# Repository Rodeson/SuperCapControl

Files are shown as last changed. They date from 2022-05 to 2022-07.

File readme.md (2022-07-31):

README For SuperCapControl

超级电容 ultracapacitor

@Rodeson

Email：lds947003754@outlook.com

## 0.超级电容图片说明

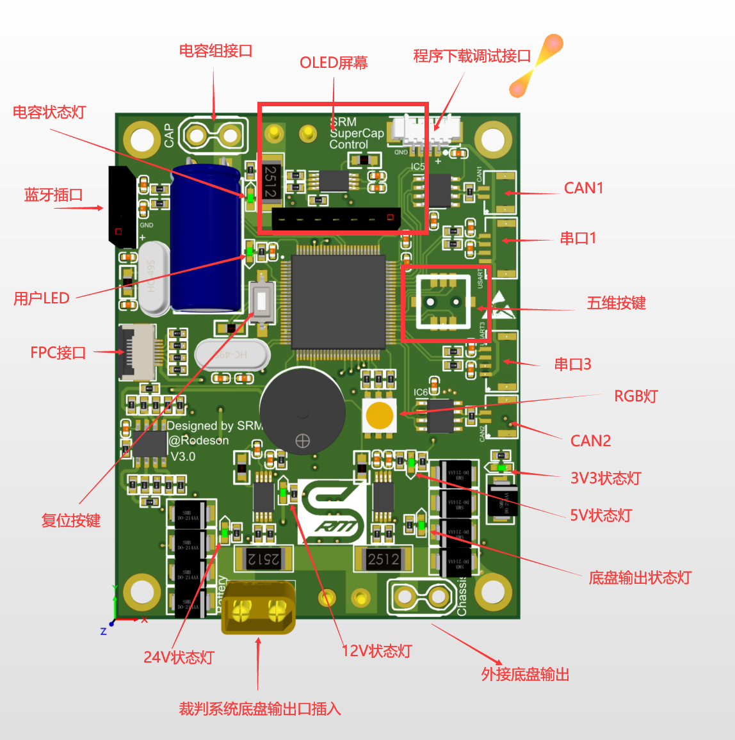
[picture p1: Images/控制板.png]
控制板
### 控制板

### 功率板

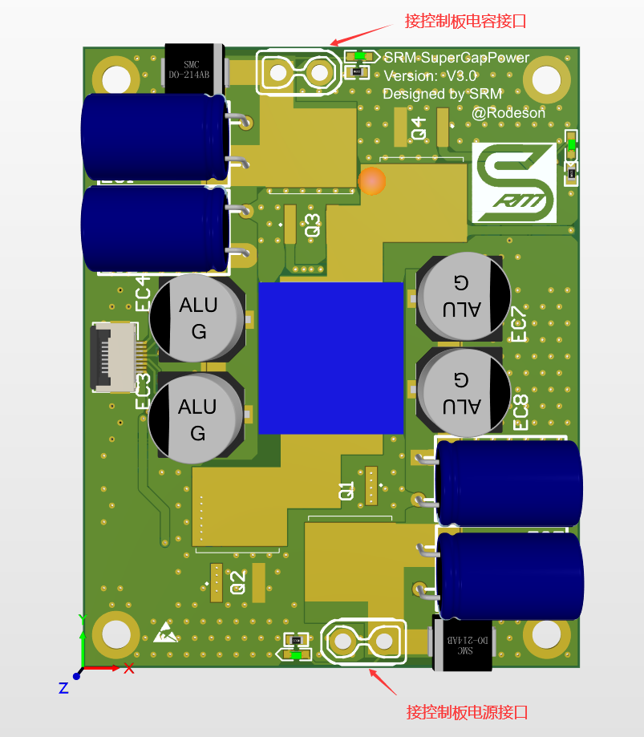
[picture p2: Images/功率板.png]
功率板


### 组合渲染图像

控制板功率板

SuperCapPCB

电容组

capacitor

## 1.超级电容硬件说明

1. 使用4Buckboost电路，实现升降压控制。
2. 将控制板和功率板进行拆分设计，两个板子对应接口固定，PWM控制线通过FPC排线连接，电源接口使用XT30接口连接。
3. 更改设计后，V2.0板子实际面积更小，在舵轮上安装方便。
4. 在实际使用过程中，为方便了解超级电容工作状态，视觉上增加RGB灯显示板子工作情况，听觉上增加蜂鸣器，能够在工作异常时第一时间了解情况。
5. 传感器选型上使用ina240a1和opa2350ua，使用adc读取模拟信号，上一代超级电容使用ina226容易出现i2c通信掉线情况。
6. 增加板载温度传感器MCP9700AT-E_TT，监测超级电容工作温度。
7. PCB设计时，减小PCB上大电流走线距离，板载大电流开窗布线。
8. 增加可交互的五维按键和OLED显示屏，方便现场调参。

## 2.硬件设计

### 2.1 采样电路

2.1.1接口采样电路

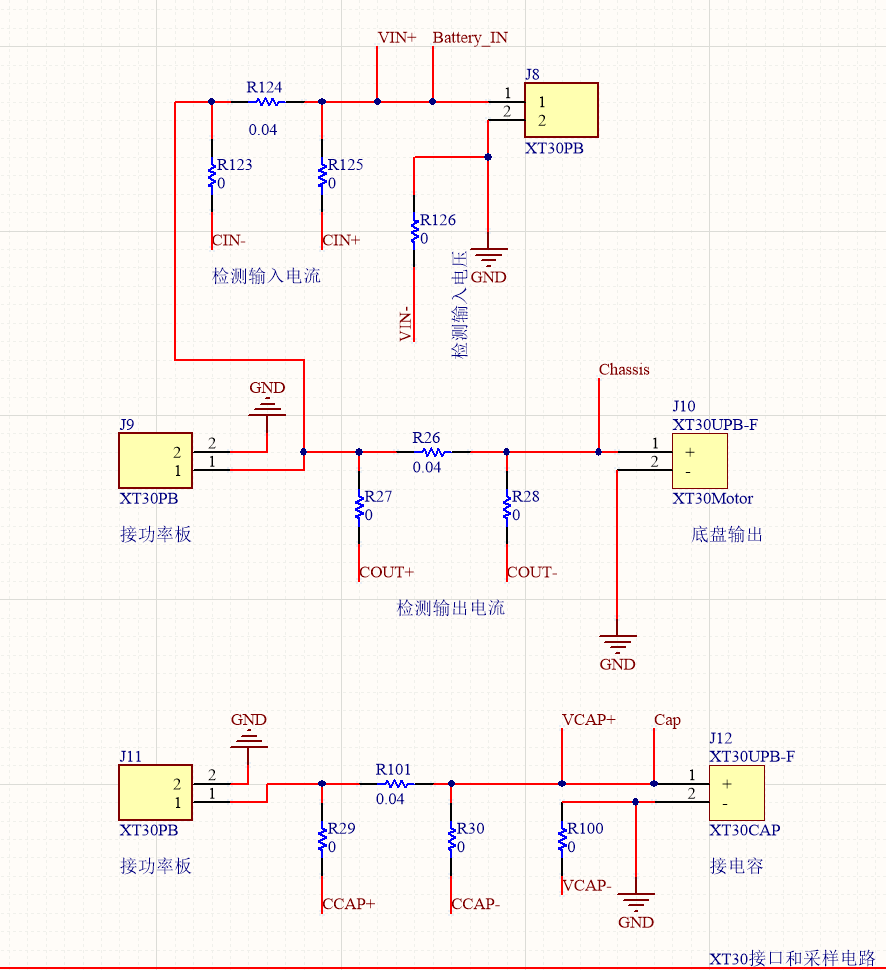
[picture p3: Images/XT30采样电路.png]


2.1.2电流传感器

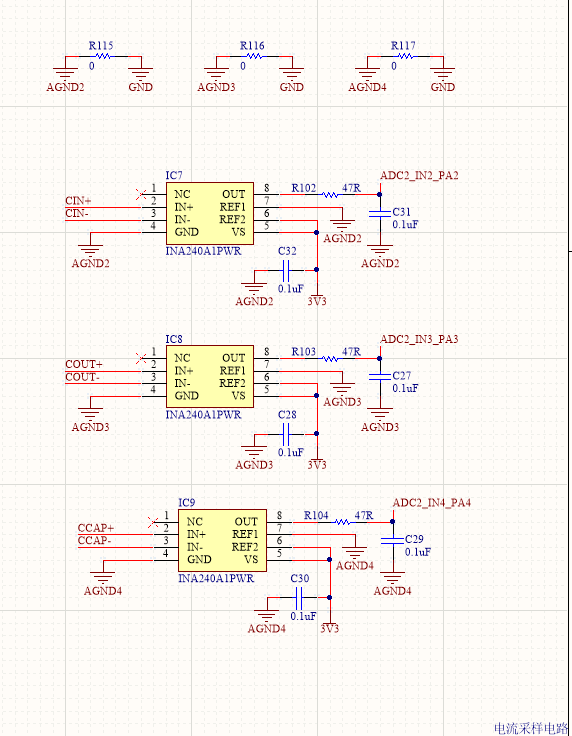
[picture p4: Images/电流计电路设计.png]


2.1.3电压传感器

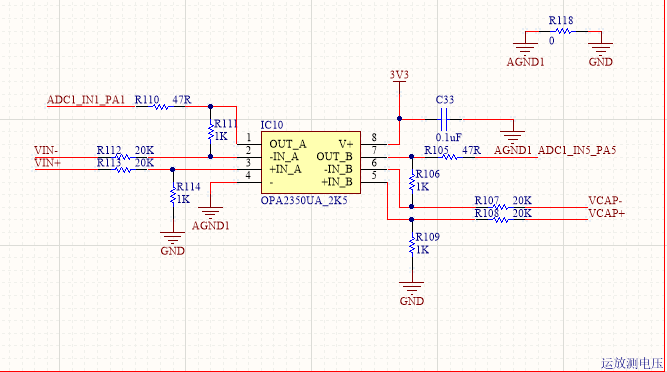
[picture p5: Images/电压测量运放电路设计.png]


### 2.2 BuckBoost电路

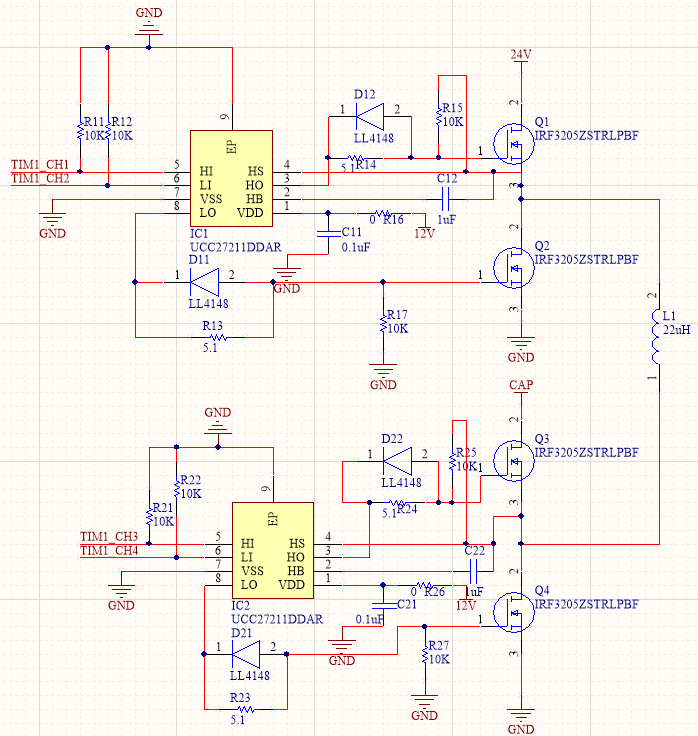
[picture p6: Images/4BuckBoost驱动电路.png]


### 2.3供电路径

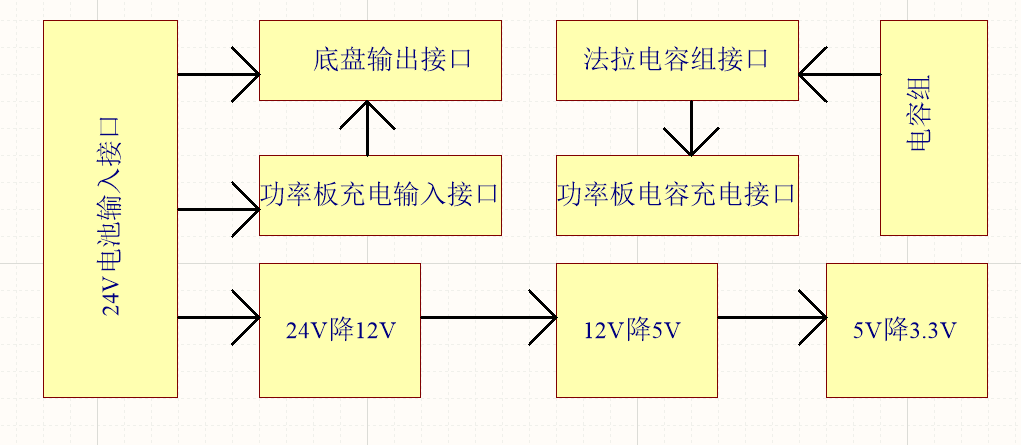
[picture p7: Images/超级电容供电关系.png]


## 3.超级电容控制思路

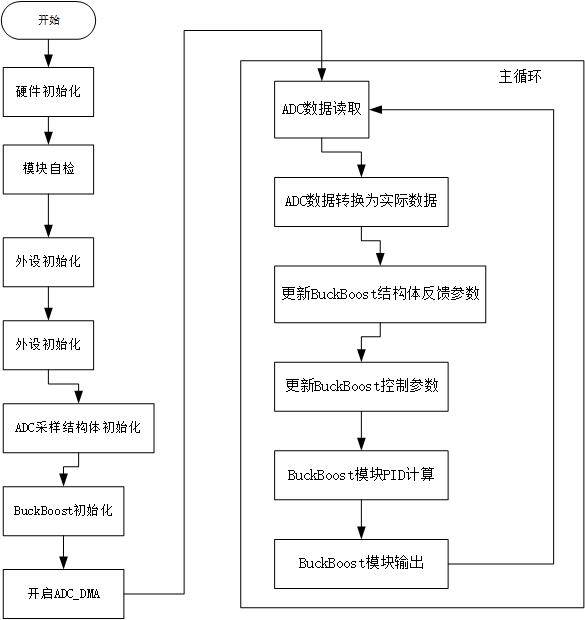
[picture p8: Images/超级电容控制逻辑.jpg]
超级电容控制逻辑


## 4.超级电容buckboost模块控制逻辑

### 4.1采样数据计算

```c
    battery_in.I_now = buckboost_control.BUCKBOOST_IN_C;
    battery_in.U_now = buckboost_control.BUCKBOOST_IN_V;
    battery_in.P_now = battery_in.I_now * battery_in.U_now;

    chassis_out.I_now = buckboost_control.BUCKBOOST_OUT_C;
    chassis_out.U_now = buckboost_control.BUCKBOOST_IN_V;
    chassis_out.P_now = chassis_out.I_now * chassis_out.U_now;

    dcdc_in.I_now = buckboost_control.BUCKBOOST_IN_C - buckboost_control.BUCKBOOST_OUT_C;
    dcdc_in.U_now = buckboost_control.BUCKBOOST_IN_V;
    dcdc_in.P_now = dcdc_in.I_now * dcdc_in.U_now;

    dcdc_out.I_now = buckboost_control.BUCKBOOST_CAP_C;
    dcdc_out.U_now = buckboost_control.BUCKBOOST_CAP_V;
    dcdc_out.P_now = buckboost_control.BUCKBOOST_CAP_C * buckboost_control.BUCKBOOST_CAP_V;
```

### 4.2串级PID思路

#### 4.2.1缓冲能量环

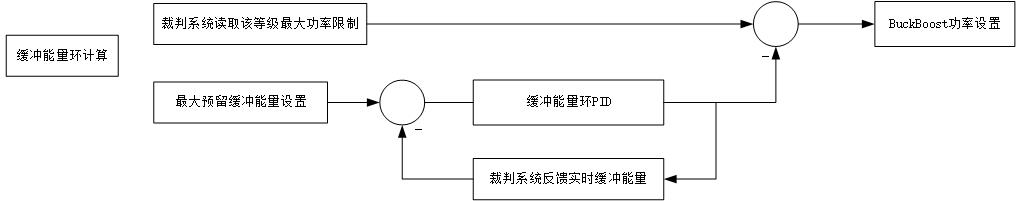
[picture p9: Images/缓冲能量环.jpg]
缓冲能量环


#### 4.2.2功率环

功率环

#### 4.2.3电压电流环

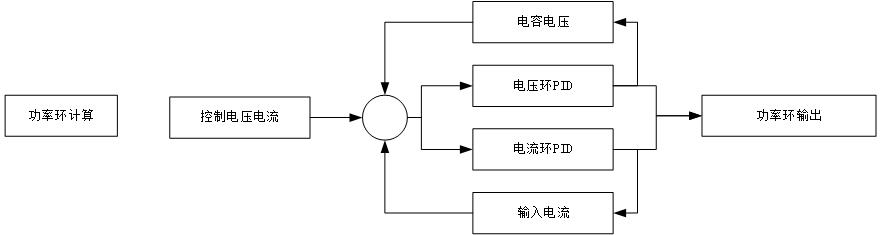
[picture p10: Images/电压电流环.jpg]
电压电流环


### 4.3输出设置

输出设置

## 5.NMOS挂载情况

```c
/****************************
24V                 CAP
Q1------|     |------Q3
        |-----|
        |  L  |
        |-----|
Q2------|     |------Q4
*****************************/
#define Q1_PWMControl_TIM     htim1
#define Q1_PWMControl_TIM_CH  TIM_CHANNEL_1
#define Q2_PWMControl_TIM     htim1
#define Q2_PWMControl_TIM_CH  TIM_CHANNEL_2
#define Q3_PWMControl_TIM     htim1
#define Q3_PWMControl_TIM_CH  TIM_CHANNEL_3
#define Q4_PWMControl_TIM     htim1
#define Q4_PWMControl_TIM_CH  TIM_CHANNEL_4
```

## 6.BuckBoost控制 C语言结构体

```c
typedef struct
{
  uint8_t data_update;    //1更新
  uint8_t buckboostmode;  //0为初始关闭模式 1为降压模式 2为升压模式
  uint8_t loop_mode;      //环路模式0：cv 1：cc 2：cp
  float efficiency;       //总效率 ，热耗散
  uint8_t power_dir;      //能量方向0正向充电1反向放电
  uint16_t max_power_lim; //裁判系统最大功率
  float power_pass;       //  裁判系统花去功率板与板子测量误差经过pid结果用于传递
  uint8_t referee_power;
  uint8_t referee_buff;
  float powerbuffer ;     //缓冲能量
    
  PID_Regulator_t BuckBoostLoopCcompare_PID;//输出电流环
  PID_Regulator_t BuckBoostLoopVcompare_PID;//输出电压环
  PID_Regulator_t Robot_Buffer_PID;//缓冲能量环
  PID_Regulator_t Robot_Power_PID;//功率环

  double BUCKBOOST_CAP_C;
  double BUCKBOOST_CAP_V;
  double BUCKBOOST_IN_C;
  double BUCKBOOST_IN_V;
  double BUCKBOOST_OUT_C;
    
  double BUCKBOOST_NEED_C;
        
  float BUCKBOOST_IN_P;
  float BUCKBOOST_OUT_P;
  float BUCKBOOST_CAP_P;
  float BUCKBOOST_NEED_P;
  
  float charge_power;//功率环计算OUT
  float charge_current;// = charge_power/inV
  float cloop;
  float vloop;
  float ratio_pass;//计算升降压比例

  uint8_t POWER_LIMIT_MODE;//超级电容功率限制模式 0使用电容 1不使用电容
    
} BUCKBOOST_STRUCT;
```

## 7.超级电容模块通信协议

### 7.1CAN 发送程序参考

发送函数

```c
void supercap_sendmessage(uint16_t Vcap)
{
		static uint8_t supercap_tx_data[2];
	
		Tx1Message.StdId=0x211;
		Tx1Message.IDE =CAN_ID_STD;
		Tx1Message.RTR=CAN_RTR_DATA;
		Tx1Message.DLC =0x08;
		memcpy (supercap_tx_data, &Vcap, sizeof(Vcap));
		HAL_CAN_AddTxMessage(&hcan1, &Tx1Message, supercap_tx_data ,&pTxMailbox);
}
```

实例应用（发送超级电容电压数据 由于是无符号16位整数 因此需要将浮点数乘以1000并发送整数）

```c
supercap_sendmessage(buckboost_control.BUCKBOOST_CAP_V * 1000);
```

### 7.2CAN 接收程序参考

接收函数（接收裁判系统底盘参数 为当前等级底盘最大功率及实时缓冲能量）

```c
void get_supercap_measure(BUCKBOOST_STRUCT *cap, uint8_t aData[])
{
    cap -> referee_power  = aData[0];
    cap -> referee_buff  = aData[1];
}
```

实例应用（该函数 扔在can线接收中断里面）

```c
void CAN1_Getdata(CAN_RxHeaderTypeDef *pHeader,uint8_t aData[])
{
	switch (pHeader->StdId)
	{
		case 0x0210:
		{
			//得到超级电容数据
			get_supercap_measure(&buckboost_control,aData);
		}
		default:
		{
			
		}break;
	}
}
```

## Bug记录

20220731 舵轮No.3 贺道明

问题描述：超级电容上电后，裁判系统电源管理模块直接停止工作，所有供电全部断掉，出现短路现象。但后续重新上电，超级电容模块恢复正常使用。

问题分析：长时间未使用超级电容，导致超级电容电压低于12V。后续上电过程中，进入大电流充电模式，导致电池输出电流较大，电池管理误判断电池短路，触发电池保护机制，断掉电池输出。

问题解决方法：临时解决方法，使用超级电容前，确保超级电容电压高于12V。后续解决方法，程序判断超级电容电压，增加电容低电压充电模式，避免上电后大电流充电。（仅限于长时间未使用，电容组电压过低情况）。

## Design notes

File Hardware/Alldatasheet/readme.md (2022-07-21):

ALLdatasheet 说明

| IC | | |
| --- | --- | ---- |
| INA225AIDGK | 电流检测芯片 | |
| LMR14020SDDAR | 24V降12V | |
| MP1584EN-LF | 12V降5V | |
| OPA2350UA_2K5 | 运放测电压 | |
| SN65HVD230DR  | CAN线接收 | |
| | | |

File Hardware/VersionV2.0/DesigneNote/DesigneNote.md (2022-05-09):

# DesigneNote

本文档记录设计过程需要修改的地方

Product：SupercapV3Control

Version：20220222

Todo：

1. OLED屏幕换成TFT屏幕 节省空间
2. 减少板载LED个数
3. 将拨码开关换成5维按键

Product：SupercapV3Control

Version：20220224

Update：

1. 新加温度传感器
2. 将拨码开关修改为五维按键
3. 补充MCU五维按键引脚
4. 3V3降压前增加测量点 保护MCU

Product：SupercapV3Power

Version：20220224 

Update：

1. 根据上版本功率板绘制原理图
2. 将排针排母走控制信号方案改为FPC走信号线方案

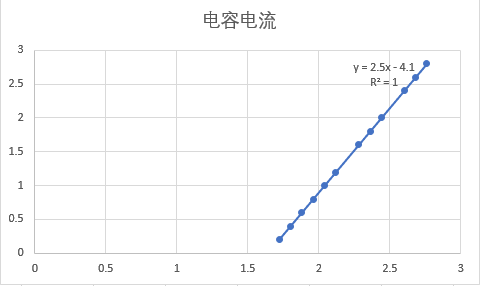
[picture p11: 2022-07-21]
Docs/SupercapNo.3Data/电容电流.png

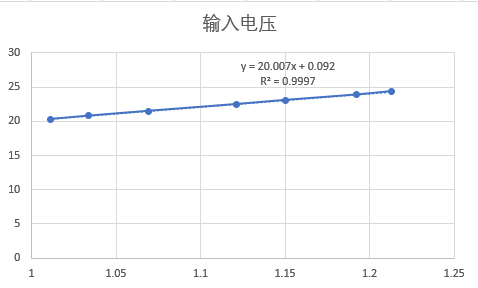
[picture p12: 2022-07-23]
Docs/SupercapNo.7Data/输入电压.png

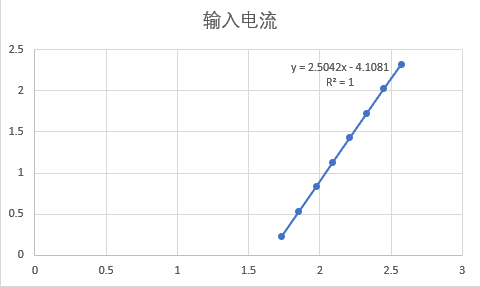
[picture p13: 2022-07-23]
Docs/SupercapNo.7Data/输入电流.png

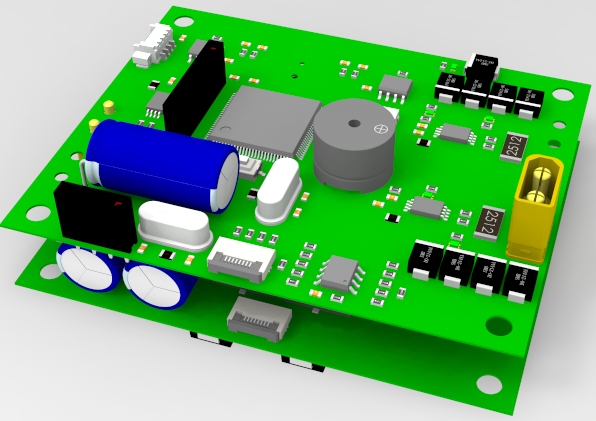
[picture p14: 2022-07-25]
Images/组合渲染图.png

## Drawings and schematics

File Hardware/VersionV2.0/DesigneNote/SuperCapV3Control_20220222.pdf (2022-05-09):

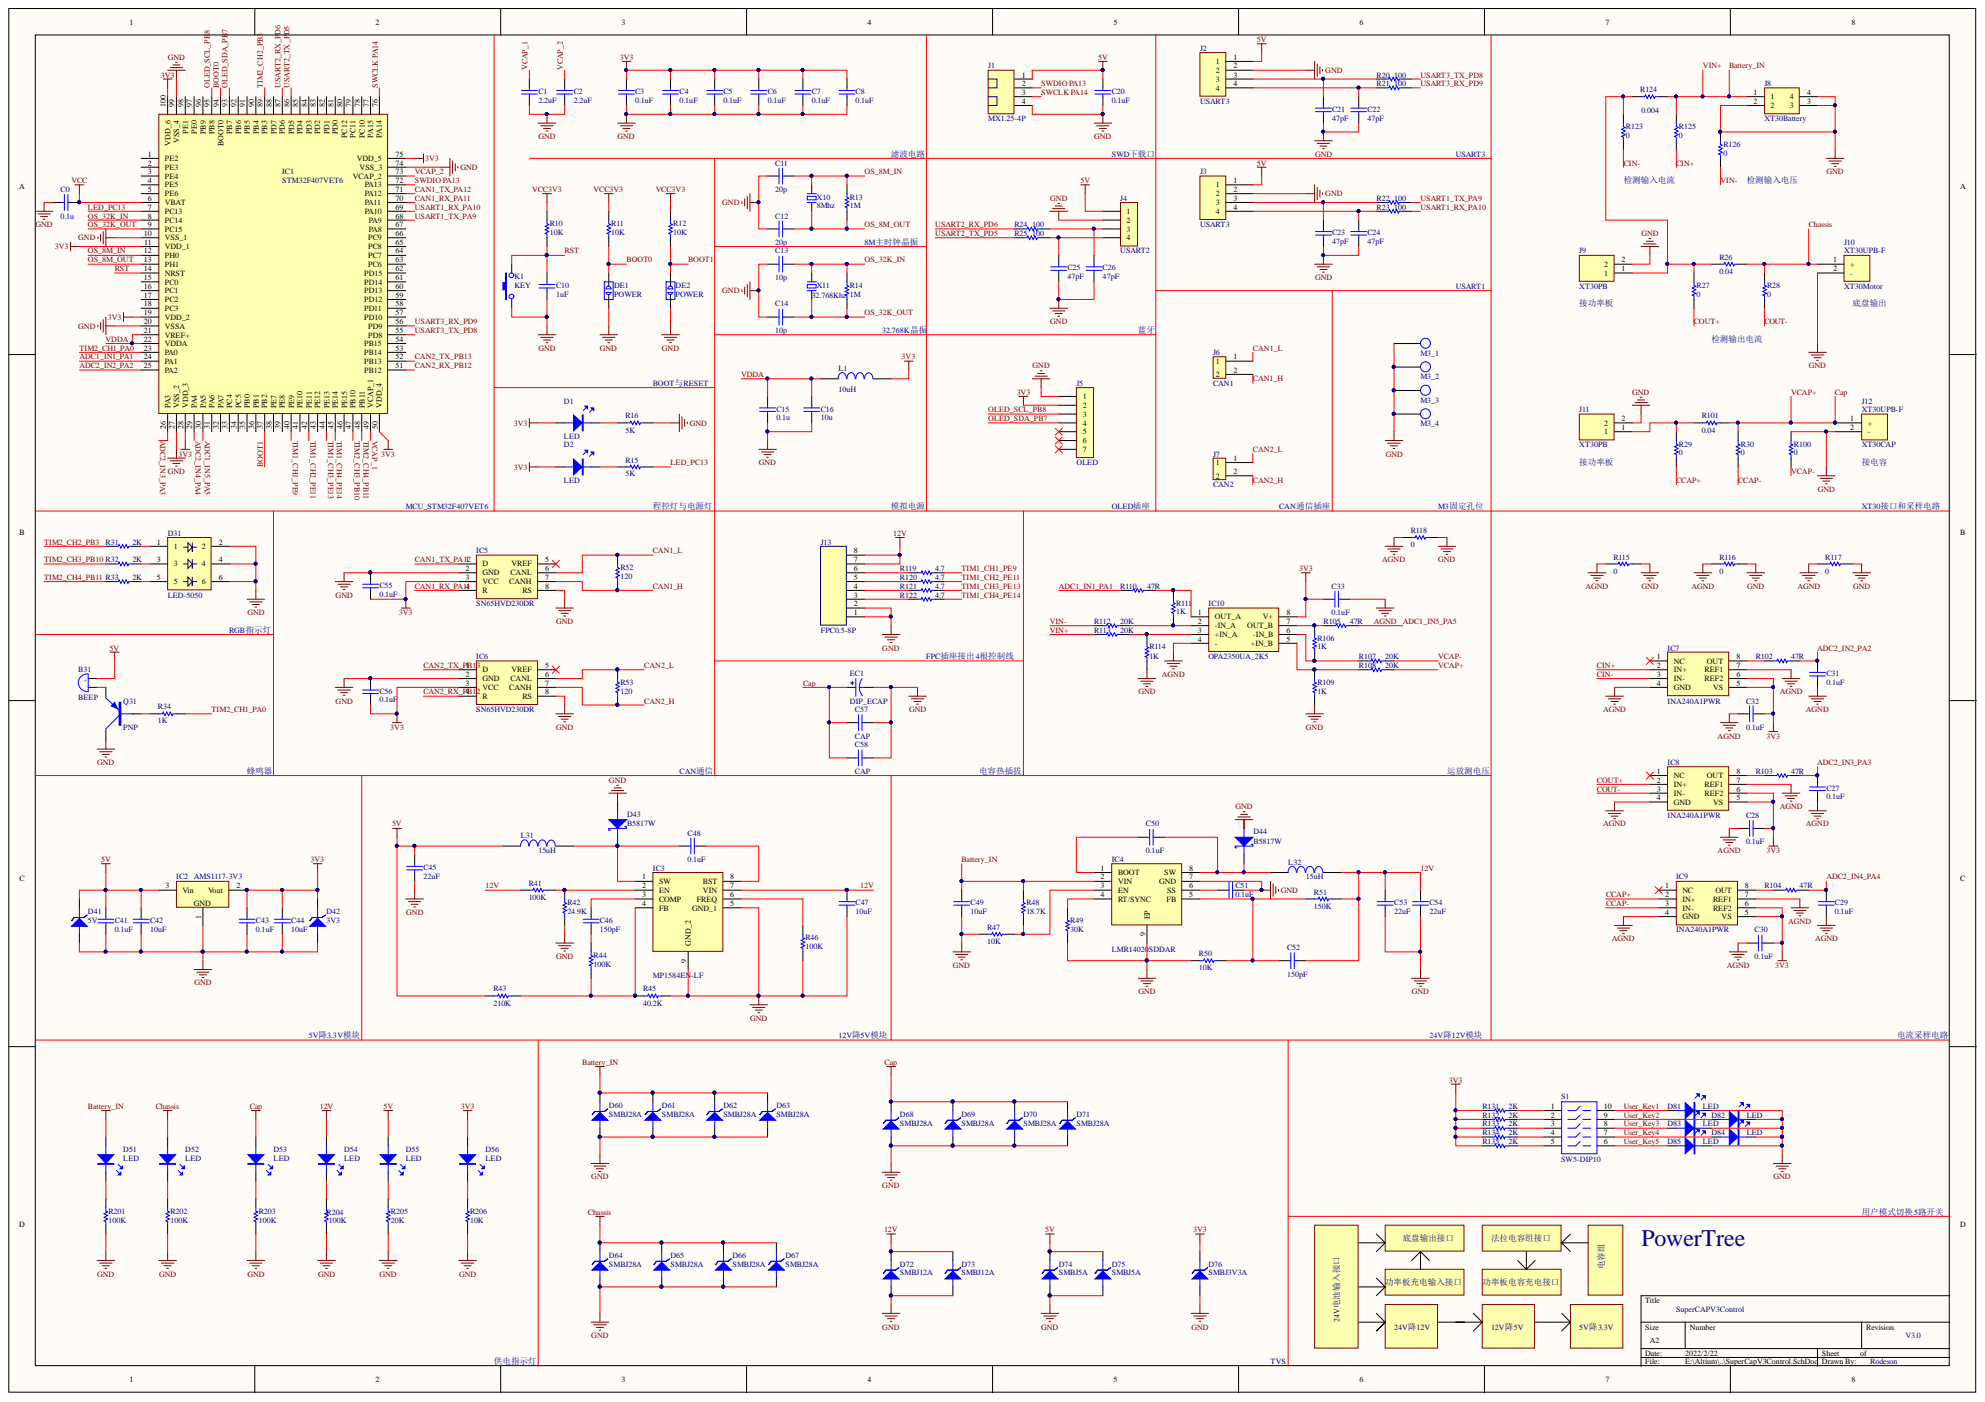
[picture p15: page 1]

User_Key5 D85 | LED

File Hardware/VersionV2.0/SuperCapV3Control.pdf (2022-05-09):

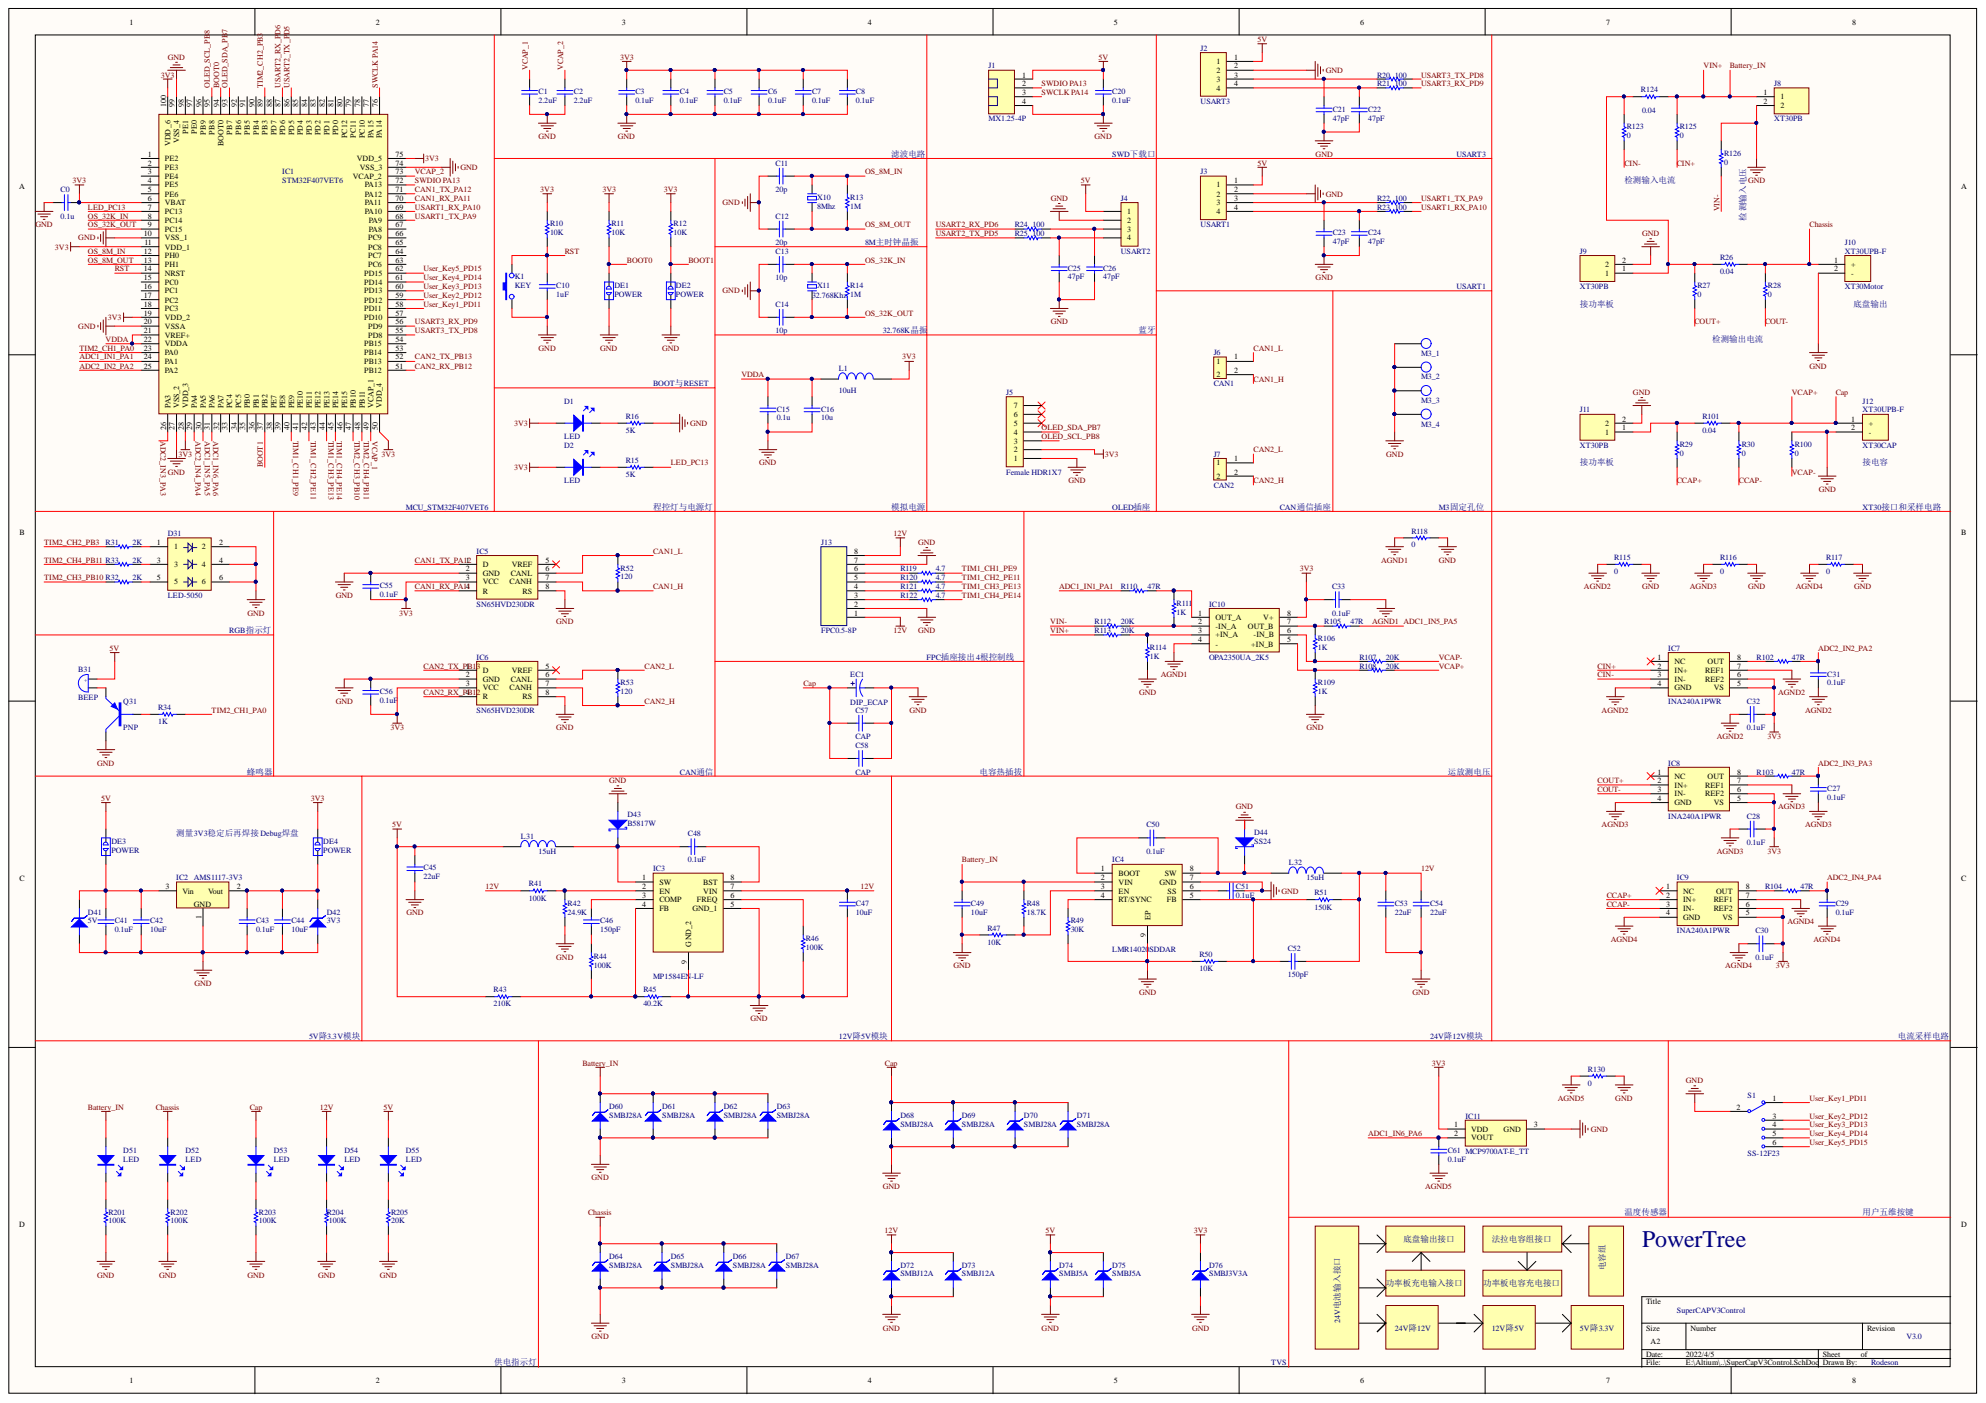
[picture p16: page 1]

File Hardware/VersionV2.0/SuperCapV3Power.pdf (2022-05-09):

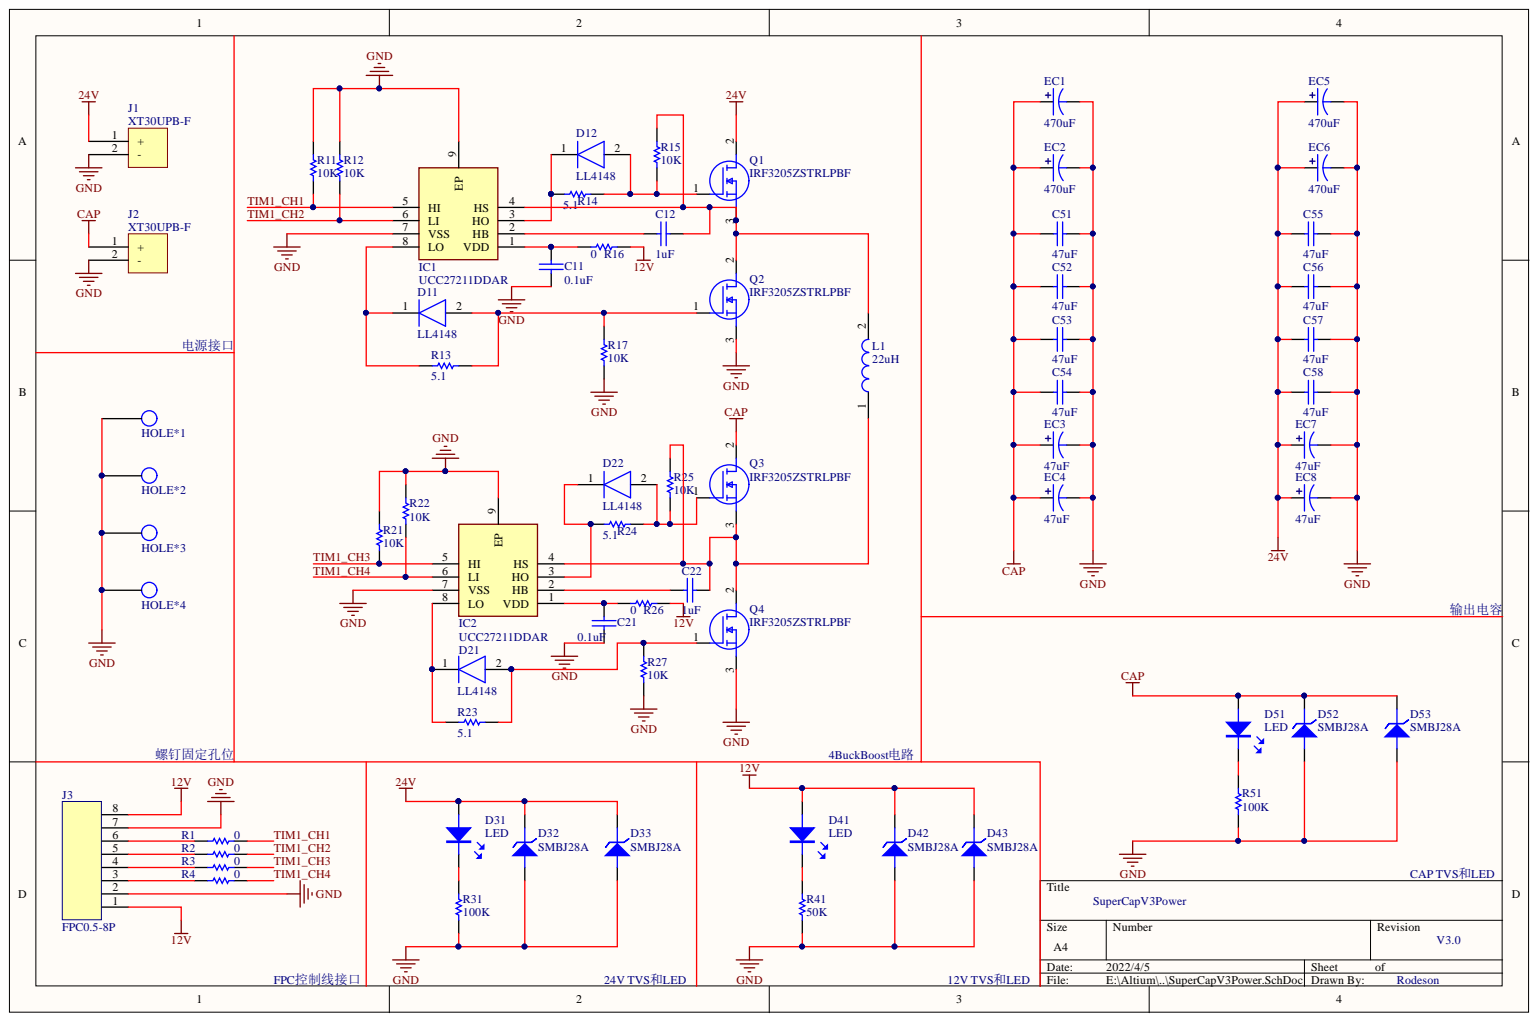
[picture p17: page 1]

D 5 1 L E D | D 5 2 SMBJ 2 8 A

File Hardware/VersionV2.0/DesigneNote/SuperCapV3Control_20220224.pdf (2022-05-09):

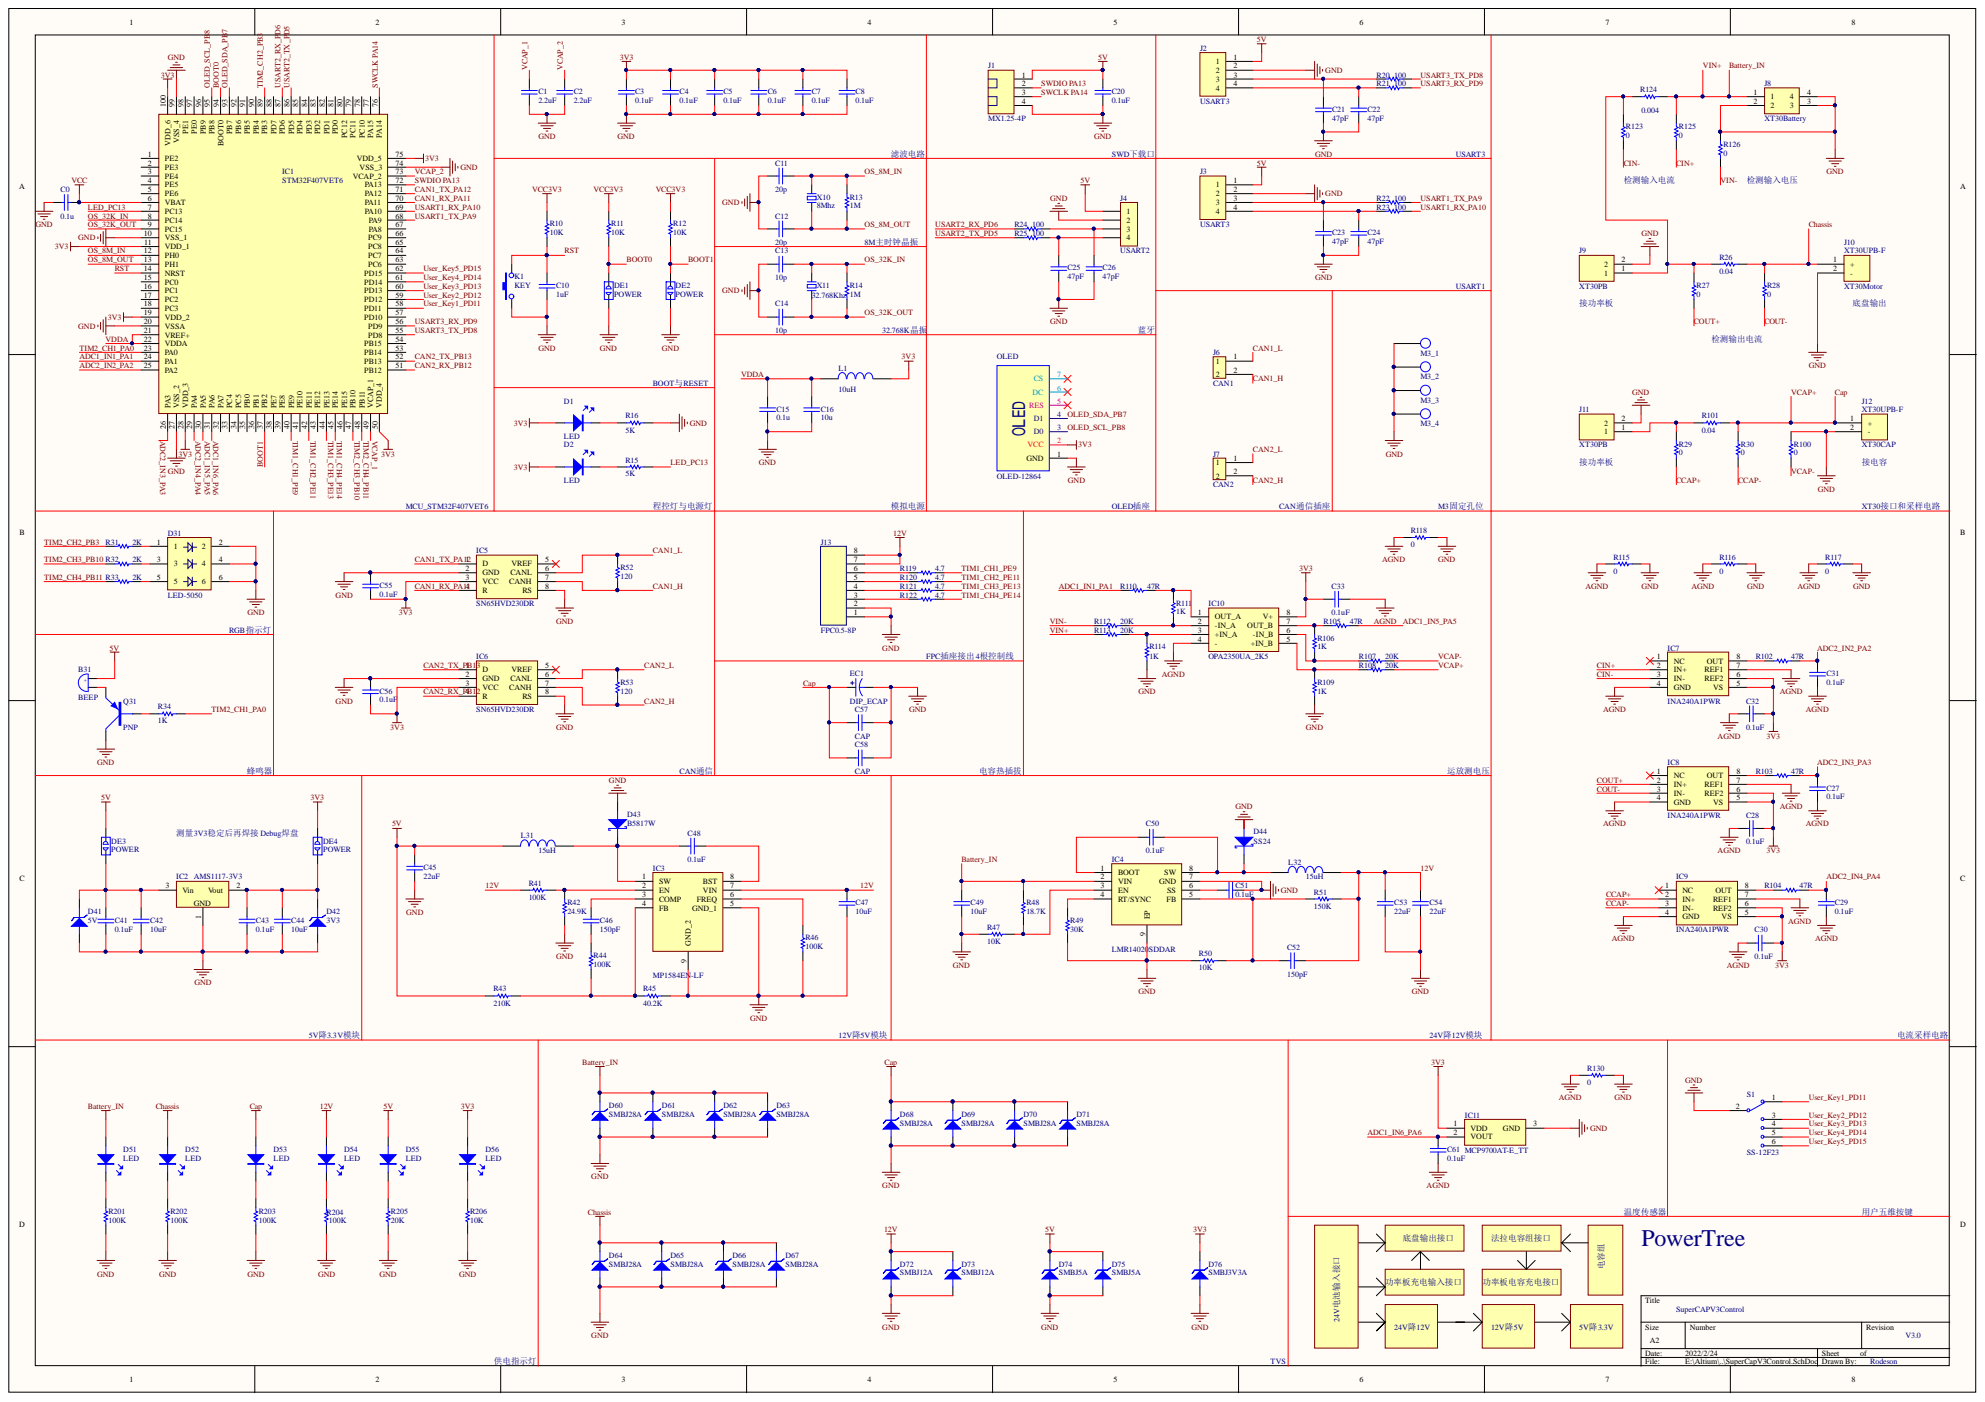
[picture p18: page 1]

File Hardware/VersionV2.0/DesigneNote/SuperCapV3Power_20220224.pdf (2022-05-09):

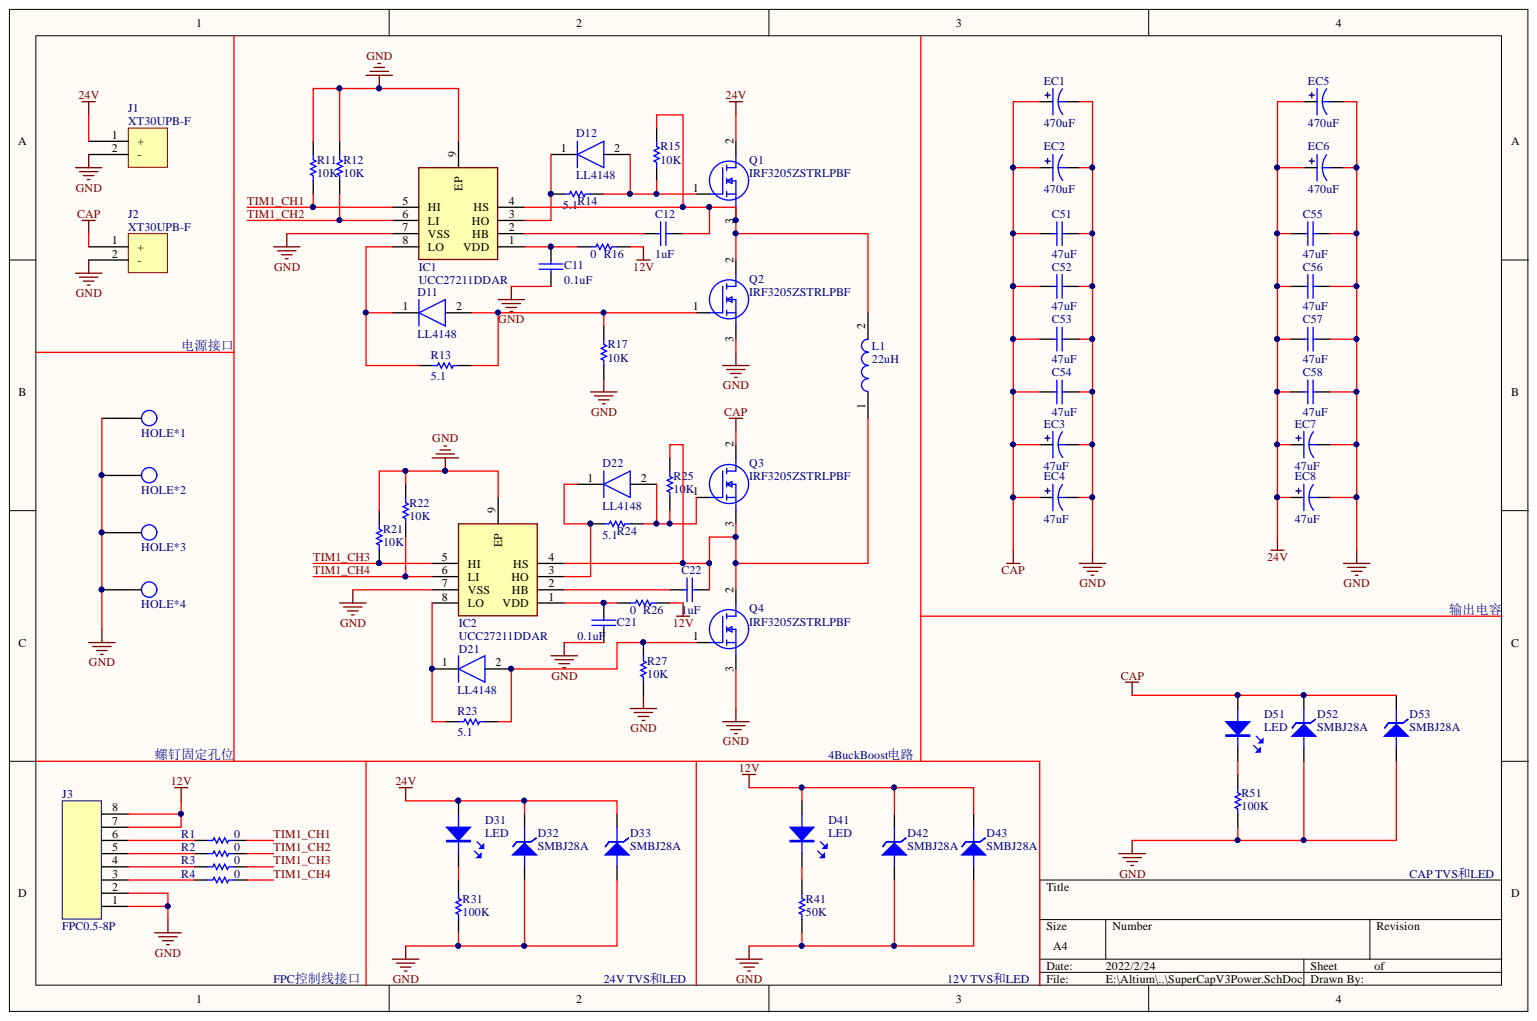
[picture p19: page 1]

D 5 1 L E D | D 5 2 SMBJ 2 8 A

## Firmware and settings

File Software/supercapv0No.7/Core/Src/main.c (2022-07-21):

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
/* Includes ------------------------------------------------------------------*/
#include "main.h"
#include "adc.h"
#include "can.h"
#include "dma.h"
#include "i2c.h"
#include "tim.h"
#include "usart.h"
#include "gpio.h"

/* USER CODE BEGIN Includes */
#include "BuckboostControl.h"
#include "RGBLED.h"
#include "buzzer.h"
#include "ADCRead.h"
#include "can_receive.h"
/* USER CODE END Includes */


void SystemClock_Config(void);
/* USER CODE BEGIN 0 */
uint32_t ADC1_Read_DMA[2];
uint32_t ADC2_Read_DMA[3];
float ADC_DATA[5];



void sendware(void *wareaddr, uint32_t waresize)
{
	#define CMD_WARE     3
	uint8_t cmdf[2] = {CMD_WARE, ~CMD_WARE};    
	uint8_t cmdr[2] = {~CMD_WARE, CMD_WARE};   
	HAL_UART_Transmit(&huart1, (uint8_t *)cmdf, sizeof(cmdf), 5000);
	HAL_UART_Transmit(&huart1, (uint8_t *)wareaddr, waresize ,5000);
	HAL_UART_Transmit(&huart1, (uint8_t *)cmdr, sizeof(cmdr), 5000);
}

void senddebug(void)
{
    float debug_data[8];
    debug_data[0] = buckboost_control.BUCKBOOST_CAP_V;
    
    debug_data[1] = buckboost_control.Robot_Power_PID.set;
    debug_data[2] = buckboost_control.Robot_Power_PID.fdb;
    
    debug_data[3] = buckboost_control.ratio_pass;
    debug_data[4] = buckboost_control.BuckBoostLoopCcompare_PID.out;
    
    debug_data[5] = buckboost_control.BuckBoostLoopCcompare_PID.set;
    debug_data[6] = buckboost_control.BuckBoostLoopCcompare_PID.fdb;
    
    debug_data[7] = buckboost_control.charge_power;
    sendware(debug_data,sizeof(debug_data));
}
/* USER CODE END 0 */

/**
  * @brief  The application entry point.
  * @retval int
  */
int main(void)
{
  /* MCU Configuration--------------------------------------------------------*/

  /* Reset of all peripherals, Initializes the Flash interface and the Systick. */
  HAL_Init();

  /* Configure the system clock */
  SystemClock_Config();

  /* Initialize all configured peripherals */
  MX_GPIO_Init();
  MX_DMA_Init();
  MX_ADC1_Init();
  MX_ADC2_Init();
  MX_I2C1_Init();
  MX_TIM1_Init();
  MX_TIM2_Init();
  MX_USART1_UART_Init();
  MX_USART2_UART_Init();
  MX_USART3_UART_Init();
  MX_CAN1_Init();
  /* USER CODE BEGIN 2 */
  HAL_GPIO_WritePin(LED_GPIO_Port,LED_Pin,GPIO_PIN_SET);
  HAL_TIM_Base_Start(&htim1);
  Buzzer_Init();
  RGB_LED_Init();
  CAN1_Init();
  //开机蜂鸣器自检
  Buzzer_BeforeWork_Check();
  //开机RGB灯自检
  RGB_LED_BeforeWork_Check();
  //开启ADC
  HAL_ADC_Start(&hadc1);
  HAL_Delay(5);
  HAL_ADC_Start(&hadc2);
  HAL_Delay(5);
  //ADC数据结构体初始化
  ELEC_INFO_INIT();
  ELEC_INFO_ADC_Read_Init();
  HAL_Delay(200);
  ELEC_INFO_ADC_Read();
  ADCDATA_To_RealDATA();

  BuckBoostInit();
  
  /* USER CODE END 2 */

  /* Infinite loop */
  /* USER CODE BEGIN WHILE */
  uint16_t loop_cnt = 0;
  uint16_t cansenddata_time_cnt = 0; 

  BuckBoostInit();
  HAL_Delay(1000);
  for(uint8_t i=0; i<10;i++)
  {
      ELEC_INFO_ADC_Read();
      ADCDATA_To_RealDATA();
      HAL_ADC_Stop_DMA(&hadc1);
      HAL_ADC_Stop_DMA(&hadc2);
      HAL_Delay(100);
  }
  
  while (1)
  {
    /* USER CODE END WHILE */

    /* USER CODE BEGIN 3 */
      
      //HAL_Delay(500);
      
      // buckboost_control.buckboostmode = 2;
      // BuckBoost_OUTControl(950);
      
      ELEC_INFO_ADC_Read();
      ADCDATA_To_RealDATA();

      BuckBoost_FIFO_Feedback();
      BuckBoost_Set_Control();
      BuckBoost_PID_Calculate();
      BuckBoost_OUT();
      
//      printf("VIN  is %.4f V\r\n",in_v.real_valu1);
//      printf("CIN  is %.4f A\r\n",in_c.real_valu1);
//      printf("COUT is %.4f A\r\n",out_c.real_valu1);
//      printf("CCAP is %.2f V\r\n",cap_c.real_valu1);
//      printf("VCAP is %.4f V\r\n",cap_v.real_valu1);
//      printf("/*********************/\r\n");
      
      HAL_ADC_Stop_DMA(&hadc1);
      HAL_ADC_Stop_DMA(&hadc2);

      loop_cnt ++;
      cansenddata_time_cnt++;
      if(loop_cnt >= 1000)
      {
          HAL_GPIO_TogglePin(LED_GPIO_Port,LED_Pin);
          loop_cnt = 0;
      }
      if(cansenddata_time_cnt >= 10)
      {
          supercap_sendmessage(buckboost_control.BUCKBOOST_CAP_V * 1000);
          cansenddata_time_cnt = 0;
      }
      //senddebug();
      //HAL_Delay(1);
  }
  /* USER CODE END 3 */
}

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
/* USER CODE BEGIN 4 */
#ifdef __GNUC__
/* With GCC, small printf (option LD Linker->Libraries->Small printf
   set to 'Yes') calls __io_putchar() */
#define PUTCHAR_PROTOTYPE int __io_putchar(int ch)
#else
#define PUTCHAR_PROTOTYPE int fputc(int ch, FILE *f)
#endif /* __GNUC__ */

typedef struct __FILE FILE;
PUTCHAR_PROTOTYPE
{
    HAL_UART_Transmit(&huart1 , (uint8_t *)&ch, 1, 0xFFFF);
    return ch;
}
/* USER CODE END 4 */
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


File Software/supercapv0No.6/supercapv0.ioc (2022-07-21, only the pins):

Mcu.UserName=STM32F407VETx
PA0-WKUP.Signal=S_TIM2_CH1_ETR
PA1.Signal=ADCx_IN1
PA10.Signal=USART1_RX
PA11.Signal=CAN1_RX
PA12.Signal=CAN1_TX
PA13.Signal=SYS_JTMS-SWDIO
PA14.Signal=SYS_JTCK-SWCLK
PA15.GPIO_Label=Key
PA15.Signal=GPXTI15
PA2.Signal=ADCx_IN2
PA3.Signal=ADCx_IN3
PA4.Signal=ADCx_IN4
PA5.Signal=ADCx_IN5
PA9.Signal=USART1_TX
PB10.Signal=S_TIM2_CH3
PB11.Signal=S_TIM2_CH4
PB3.Signal=S_TIM2_CH2
PB7.GPIO_Label=OLED_SDA
PB7.Signal=I2C1_SDA
PB8.GPIO_Label=OLED_SCL
PB8.Signal=I2C1_SCL
PC13-ANTI_TAMP.GPIO_Label=LED
PC13-ANTI_TAMP.Signal=GPIO_Output
PD5.Signal=USART2_TX
PD6.Signal=USART2_RX
PD8.Signal=USART3_TX
PD9.Signal=USART3_RX
PE11.Signal=S_TIM1_CH2
PE13.Signal=S_TIM1_CH3
PE14.Signal=S_TIM1_CH4
PE9.Signal=S_TIM1_CH1
PH0-OSC_IN.Signal=RCC_OSC_IN
PH1-OSC_OUT.Signal=RCC_OSC_OUT

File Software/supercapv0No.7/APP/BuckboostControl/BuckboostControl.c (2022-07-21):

#include "BuckboostControl.h"

BUCKBOOST_STRUCT buckboost_control;

CONTROL_STRUCT battery_in;
CONTROL_STRUCT chassis_out;
CONTROL_STRUCT dcdc_in;
CONTROL_STRUCT dcdc_out;

//BuckBoost电路PWM初始化
void BuckBoostInit(void)
{
    HAL_TIM_Base_Start(&htim1);
    HAL_TIM_PWM_Start(&Q1_PWMControl_TIM,Q1_PWMControl_TIM_CH);
    HAL_TIM_PWM_Start(&Q2_PWMControl_TIM,Q2_PWMControl_TIM_CH);
    HAL_TIM_PWM_Start(&Q3_PWMControl_TIM,Q3_PWMControl_TIM_CH);
    HAL_TIM_PWM_Start(&Q4_PWMControl_TIM,Q4_PWMControl_TIM_CH);
    
    //初始4个MOS全关
    __HAL_TIM_SetCompare(&Q1_PWMControl_TIM,Q1_PWMControl_TIM_CH,0);
    __HAL_TIM_SetCompare(&Q2_PWMControl_TIM,Q2_PWMControl_TIM_CH,1000);
    __HAL_TIM_SetCompare(&Q3_PWMControl_TIM,Q3_PWMControl_TIM_CH,1000);
    __HAL_TIM_SetCompare(&Q4_PWMControl_TIM,Q4_PWMControl_TIM_CH,0);
    //BuckBoostPID控制参数初始化
    //1.缓冲能量环
    PID_Init(&buckboost_control.Robot_Buffer_PID,
                           Robot_Buffer_PID_MODE,
                        Robot_Buffer_PID_MAX_OUT,
                       Robot_Buffer_PID_MAX_IOUT,
                             Robot_Buffer_PID_KP,
                             Robot_Buffer_PID_KI,
                             Robot_Buffer_PID_KD);    
    //2.功率环
    PID_Init(&buckboost_control.Robot_Power_PID,
                           Robot_Power_PID_MODE,
                        Robot_Power_PID_MAX_OUT,
                       Robot_Power_PID_MAX_IOUT,
                             Robot_Power_PID_KP,
                             Robot_Power_PID_KI,
                             Robot_Power_PID_KD);
    //3.电流环
    PID_Init(&buckboost_control.BuckBoostLoopCcompare_PID,
                                  BUCKBOOSTLOOPC_PID_MODE,
                               BUCKBOOSTLOOPC_PID_MAX_OUT,
                              BUCKBOOSTLOOPC_PID_MAX_IOUT,
                                    BUCKBOOSTLOOPC_PID_KP,
                                    BUCKBOOSTLOOPC_PID_KI,
                                    BUCKBOOSTLOOPC_PID_KD);
    //4.电压环
    PID_Init(&buckboost_control.BuckBoostLoopVcompare_PID,
                                  BUCKBOOSTLOOPV_PID_MODE,
                               BUCKBOOSTLOOPV_PID_MAX_OUT,
                              BUCKBOOSTLOOPV_PID_MAX_IOUT,
                                    BUCKBOOSTLOOPV_PID_KP,
                                    BUCKBOOSTLOOPV_PID_KI,
                                    BUCKBOOSTLOOPV_PID_KD);
   //滤波初始化
   for (uint8_t i = 0; i < 5; i++)
   {
       low_filter_init(&lpf[i], 10e3, 1e3);
   }
}

volatile float buck_duty = 0;
volatile float boost_duty = 0;
volatile uint32_t BB_CompareValue = 0;
volatile uint32_t BB_CompareValue_CAL= 0;
void BuckBoost_OUTControl(float ratio) // vout/vin
{    
volatile float CompareValue;    
//升降压判断        
    if(ratio < 0 && buckboost_control.power_dir == 1)
    {
        CompareValue = 0.96 * ratio * 1000;
        boost_duty = 0.06;
        buck_duty = 0.96 * ratio;
    }
    else if(ratio > 1.0f && buckboost_control.BUCKBOOST_CAP_V > buckboost_control.BUCKBOOST_IN_V)//需要升压
    {
        buckboost_control.buckboostmode = 2;
        buck_duty  = 0.05;
        boost_duty = 1 - buck_duty/ratio;
    }
    else if(ratio < 1.0f && ratio > 0)//需要降压
    {
        buckboost_control.buckboostmode = 1;
        boost_duty = 0.06;
        buck_duty  = ratio * (1 - boost_duty);
    }
    else//error ratio < 0
    {
        buckboost_control.buckboostmode = 0;
    }
    
    //超级电容电压大于最大设定电压时  关闭电流环 电压环 输出
    if(buckboost_control.BUCKBOOST_CAP_V > CAP_V_MAX && buckboost_control.power_dir == 0)
    {
        buckboost_control.buckboostmode = 0;
        buckboost_control.BuckBoostLoopCcompare_PID.out = 0;
        buckboost_control.BuckBoostLoopVcompare_PID.out = 0;
    }
    
    
    
//输出
    //放电模式
    if(buckboost_control.power_dir == 1 && buckboost_control.BUCKBOOST_CAP_V > CAP_V_MIN)
    {
        BB_CompareValue = 1000 * 0.94*buckboost_control.BUCKBOOST_CAP_V/buckboost_control.BUCKBOOST_IN_V;
        BB_CompareValue = 2 * BB_CompareValue + CompareValue;
        BB_CompareValue = BB_CompareValue / 2;
        
        if(BB_CompareValue > 950)
        {
            BB_CompareValue = 950;
        }
        else if(BB_CompareValue < 60)
        {
            BB_CompareValue = 60;
        }
      
        __HAL_TIM_SetCompare(&Q1_PWMControl_TIM,Q1_PWMControl_TIM_CH,BB_CompareValue);
        __HAL_TIM_SetCompare(&Q2_PWMControl_TIM,Q2_PWMControl_TIM_CH,BB_CompareValue);
        __HAL_TIM_SetCompare(&Q3_PWMControl_TIM,Q3_PWMControl_TIM_CH,60);
        __HAL_TIM_SetCompare(&Q4_PWMControl_TIM,Q4_PWMControl_TIM_CH,60);        
    }
    else if(buckboost_control.power_dir == 1 && buckboost_control.BUCKBOOST_CAP_V < CAP_V_MIN)
    {
        buckboost_control.BuckBoostLoopCcompare_PID.out = 0;
        __HAL_TIM_SetCompare(&Q1_PWMControl_TIM,Q1_PWMControl_TIM_CH,0);
        __HAL_TIM_SetCompare(&Q2_PWMControl_TIM,Q2_PWMControl_TIM_CH,1000);
        __HAL_TIM_SetCompare(&Q3_PWMControl_TIM,Q3_PWMControl_TIM_CH,1000);
        __HAL_TIM_SetCompare(&Q4_PWMControl_TIM,Q4_PWMControl_TIM_CH,0);        
    }
    //充电模式
    else if(buckboost_control.buckboostmode == 0)
    {
        __HAL_TIM_SetCompare(&Q1_PWMControl_TIM,Q1_PWMControl_TIM_CH,0);
        __HAL_TIM_SetCompare(&Q2_PWMControl_TIM,Q2_PWMControl_TIM_CH,1000);
        __HAL_TIM_SetCompare(&Q3_PWMControl_TIM,Q3_PWMControl_TIM_CH,1000);
        __HAL_TIM_SetCompare(&Q4_PWMControl_TIM,Q4_PWMControl_TIM_CH,0);          
    }
    else if(buckboost_control.buckboostmode == 1)
    {
        
        BB_CompareValue = BB_CompareValue + buck_duty * 1000;
        BB_CompareValue = BB_CompareValue /2;
        BB_CompareValue_CAL = 1000 * 0.94*buckboost_control.BUCKBOOST_CAP_V/buckboost_control.BUCKBOOST_IN_V;
        
        if(buckboost_control.power_dir == 0)
        {
            if(BB_CompareValue < BB_CompareValue_CAL)  BB_CompareValue = BB_CompareValue_CAL;
        }
        
        if(BB_CompareValue > 950)
        {
            BB_CompareValue = 950;
        }
        
        __HAL_TIM_SetCompare(&Q1_PWMControl_TIM,Q1_PWMControl_TIM_CH,BB_CompareValue);
        __HAL_TIM_SetCompare(&Q2_PWMControl_TIM,Q2_PWMControl_TIM_CH,BB_CompareValue);
        __HAL_TIM_SetCompare(&Q3_PWMControl_TIM,Q3_PWMControl_TIM_CH,60);
        __HAL_TIM_SetCompare(&Q4_PWMControl_TIM,Q4_PWMControl_TIM_CH,60);        
    }
    else if(buckboost_control.buckboostmode == 2)
    {
        BB_CompareValue = BB_CompareValue + boost_duty * 1000;
        BB_CompareValue = BB_CompareValue / 2;
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

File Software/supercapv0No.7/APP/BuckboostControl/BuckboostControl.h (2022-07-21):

#ifndef _BUCKBOOSTCONTROL_H
#define _BUCKBOOSTCONTROL_H


#include "main.h"
#include "tim.h"
#include "gpio.h"
#include "ADCRead.h"
#include "pid.h"
#include "supercap_config.h"
#include "filter.h"





/****************************
24V                 CAP
Q1------|     |------Q3
        |-----|
        |  L  |
        |-----|
Q2------|     |------Q4
*****************************/
#define Q1_PWMControl_TIM     htim1
#define Q1_PWMControl_TIM_CH  TIM_CHANNEL_1
#define Q2_PWMControl_TIM     htim1
#define Q2_PWMControl_TIM_CH  TIM_CHANNEL_2
#define Q3_PWMControl_TIM     htim1
#define Q3_PWMControl_TIM_CH  TIM_CHANNEL_3
#define Q4_PWMControl_TIM     htim1
#define Q4_PWMControl_TIM_CH  TIM_CHANNEL_4

typedef struct
{
  float U_now;
  float I_now;
  float P_now;
} CONTROL_STRUCT;

//电流环PID
#define BUCKBOOSTLOOPC_PID_MODE          PID_DELTA
#define BUCKBOOSTLOOPC_PID_MAX_OUT       150
#define BUCKBOOSTLOOPC_PID_MAX_IOUT      15
#define BUCKBOOSTLOOPC_PID_KP            0.4f  
#define BUCKBOOSTLOOPC_PID_KI            0.03f      
#define BUCKBOOSTLOOPC_PID_KD            0.0f 

//电压环PID
#define BUCKBOOSTLOOPV_PID_MODE          PID_DELTA
#define BUCKBOOSTLOOPV_PID_MAX_OUT       100
#define BUCKBOOSTLOOPV_PID_MAX_IOUT      15
#define BUCKBOOSTLOOPV_PID_KP            1.2f   
#define BUCKBOOSTLOOPV_PID_KI            0.06f      
#define BUCKBOOSTLOOPV_PID_KD            0.0f 

//缓冲能量环PID
#define Robot_Buffer_PID_MODE          PID_DELTA
#define Robot_Buffer_PID_MAX_OUT       5
#define Robot_Buffer_PID_MAX_IOUT      2
#define Robot_Buffer_PID_KP            0.7f     
#define Robot_Buffer_PID_KI            0.01f      
#define Robot_Buffer_PID_KD            0.0f

//功率环PID
#define Robot_Power_PID_MODE          PID_DELTA
#define Robot_Power_PID_MAX_OUT       300
#define Robot_Power_PID_MAX_IOUT      80
#define Robot_Power_PID_KP            0.35f    
#define Robot_Power_PID_KI            0.035f      
#define Robot_Power_PID_KD            0.0f


typedef struct
{
  uint8_t data_update;    //1更新
  uint8_t buckboostmode;  //0为初始关闭模式 1为降压模式 2为升压模式
  uint8_t loop_mode;      //环路模式0：cv 1：cc 2：cp
  float efficiency;       //总效率 ，热耗散
  uint8_t power_dir;      //能量方向0正向充电1反向放电
  uint16_t max_power_lim; //裁判系统最大功率
  float power_pass;       //  裁判系统花去功率板与板子测量误差经过pid结果用于传递
  uint8_t referee_power;
  uint8_t referee_buff;
  float powerbuffer ;     //缓冲能量
    
  PID_Regulator_t BuckBoostLoopCcompare_PID;//输出电流环
  PID_Regulator_t BuckBoostLoopVcompare_PID;//输出电压环
  PID_Regulator_t Robot_Buffer_PID;//缓冲能量环
  PID_Regulator_t Robot_Power_PID;//功率环
    
  
  double BUCKBOOST_CAP_C;
  double BUCKBOOST_CAP_V;
  double BUCKBOOST_IN_C;
  double BUCKBOOST_IN_V;
  double BUCKBOOST_OUT_C;
    
  double BUCKBOOST_NEED_C;
        
  float BUCKBOOST_IN_P;
  float BUCKBOOST_OUT_P;
  float BUCKBOOST_CAP_P;
  float BUCKBOOST_NEED_P;
  
  float charge_power;//功率环计算OUT
  float charge_current;// = charge_power/inV
  float cloop;
  float vloop;
  float ratio_pass;//计算升降压比例

  uint8_t POWER_LIMIT_MODE;//超级电容功率限制模式 0使用电容 1不使用电容
    
} BUCKBOOST_STRUCT;




extern BUCKBOOST_STRUCT buckboost_control;

void BuckBoostInit(void);
void BuckBoost_FIFO_Feedback(void);
void BuckBoost_Set_Control(void);
void BuckBoost_PID_Calculate(void);
void BuckBoost_OUT(void);
void BuckBoost_OUTControl(float ratio);
#endif

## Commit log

2022-01-05 首次上传
    First Update
    [MCU_Module.SchDoc, SuperCapV0.PrjPCB]
2022-01-05 Create SuperCapV0.SchDoc
    上传遗漏的功率板原理图
    [SuperCapV0.SchDoc]
2022-05-09 UpdateVersion
    更新超级电容硬件
    [MCU_Module.SchDoc, SuperCapV0.PrjPCB, SuperCapV0.SchDoc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]
2022-07-21 更新超级电容软件程序
2022-07-21 更新超级电容参数及校准文档信息
    [超级电容参数校准.xlsx]
2022-07-21 更新Readme文档及关联图片
2022-07-21 更新readme软件相关说明
2022-07-21 更新超级电容说明文档
    增添图片说明
2022-07-21 删除重复图片
2022-07-21 更新超级电容控制板No.5相关参数及硬件设计手册
    [超级电容参数校准.xlsx]
2022-07-23 更新备用板No.7程序
    目前已经在电子负载上完成No.7板子测试
2022-07-23 更新SupercapNo.7参数校正表
    更新备用板No.7参数校正表及拟合函数与图像
    [超级电容参数校准.xlsx]
2022-07-25 更新超级电容说明文档
    1. 更新控制板和功率板组合渲染图 2.更新说明文档超级电容通信部分
2022-07-25 更新渲染图像
2022-07-31 Updata readme bug part
    更新超级电容bug日志
2022-07-31 更新渲染图
    重新渲染更新 超级电容控制器 和 电容组 的渲染图
2022-08-01 Update 超级电容参数校准.xlsx
    增加电容组充电理论曲线
    [超级电容参数校准.xlsx]

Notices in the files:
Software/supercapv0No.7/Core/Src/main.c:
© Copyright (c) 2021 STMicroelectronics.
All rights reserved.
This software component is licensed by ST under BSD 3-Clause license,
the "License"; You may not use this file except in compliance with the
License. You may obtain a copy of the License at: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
